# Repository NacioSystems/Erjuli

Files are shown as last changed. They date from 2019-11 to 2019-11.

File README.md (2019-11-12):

# Erjuli

## de NacioSystems:

Versión 3.0
Fecha: 5/11/2019

Este proyecto es robot de minisumo llamado **Erjuli**, pensado para las competiciones de un máximo de 500gr y dimensiones de 10x10cm2. Realizado por NacioSystems (O Milladoiro):

Es la tercera versión de este robot, la primera participó en la Oshwdem 2016, tenía una caja de madera y una balda desplegable, En la segunda versión se cambió la caja de madera por una impresa en 3D con PLA y se le añadió un micorservo en la parte trasera, para activar un brazo que bajaba la muleta que intentaba torear a los otros robots competidores. En esta tercera versión se eliminó la balda desplegable, por otra fija de material flexible pensada para el mismo efecto y se retocó el software para adaptarlo a las tres fases de la competición

- - -

### Introducción:

El chasis del vehículo está construido sobre la plataforma **Pololu Zumo Arduino**, sobre el que se instalaron sensores de distancia a través de ultrasonidos **HC-SR04**, uno en la dirección frontal y otro a cada lado del bastidor. Se complementa con el sensor **QTR** frontal de Pololu Zumo, que tendrá la función de detectar la línea del borde de la pista, con el objeto de no salirse.

El vehículo se enciende con el interruptor de la _shield_ de _Pololu_ y queda parado a la espera de que se pulse el botón incorporado en el chasis, para iniciar el combate. Una vez pulsado el botón **Erjuli** cuenta los 5 segundos de rigor que marcan las reglas. Una vez en marcha lee a través de los sensores en que situación está el contrincante, delante, a la derecha o a la izquierda. Lógicamente si no está en ninguna de esas posiciones es que estará detrás. **Erjuli** girará en la dirección en la que encuentre al contrincante y acelerará para embestirlo con sus 500gr de peso. Si en el movimiento detecta que pisa el borde de la pista, con los sensores delanteros QTR, retrocederá para salir de la zona  de peligro.

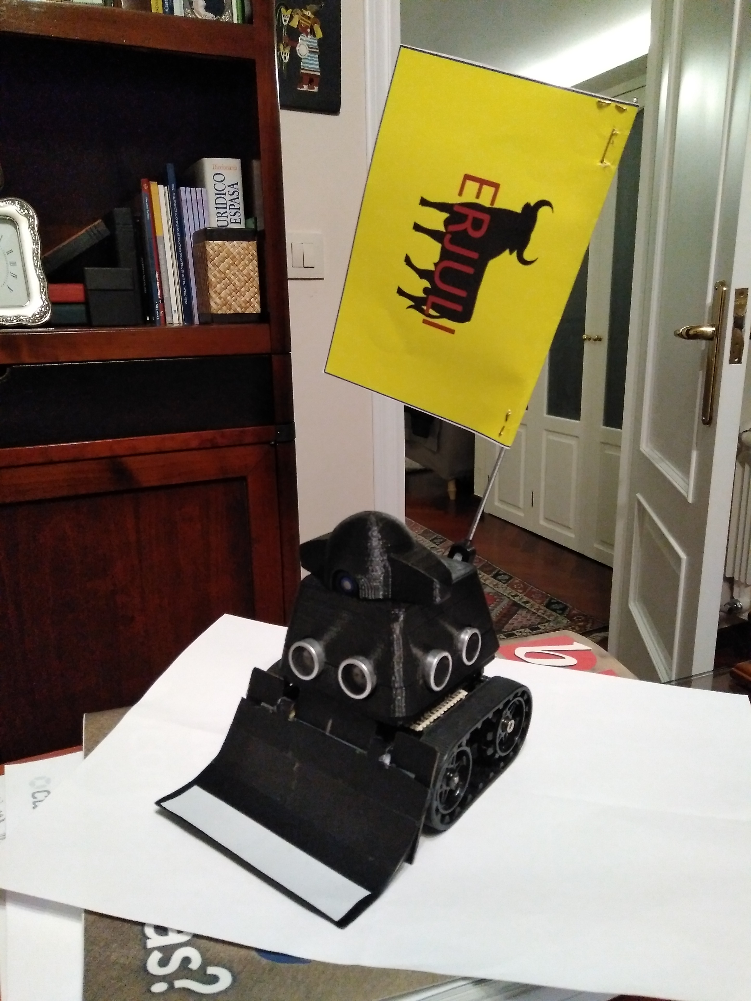
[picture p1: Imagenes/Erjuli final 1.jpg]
Erjuli Erjuli listo


Los sensores **HC-SR04** se activan simultáneamente a la vez, leyendo cada uno de ellos su propia señal y la de los otros sensores de modo sincronizado, hasta un rango de 50cm. Si detecta un objeto o contrincante en alguno de los lados, girará hasta detectarlo con el sensor frontal, pero este giro será por un tiempo limitado,para evitar quedarse en la misma posición expuesto al ataque del adversario.

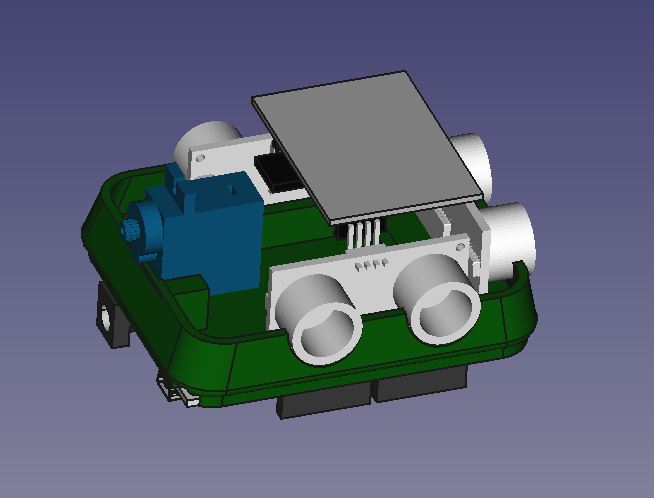
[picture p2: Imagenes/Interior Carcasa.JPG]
Sensores 3D Situación sensores


Al mismo tiempo **Erjuli** moverá su servomotor trasero, para poner la muleta del lado en que encuentra el adversario, para que este se confunda con el señuelo

### Materiales:

El vehículo utiliza los siguientes materiales:
* Pololu Zumo for Arduino con balda
* Arduino UNO R3
* 3 x HC-SR04
* Zumo Reflectante Sensor Array
* Microsergo SG90
* Piezas impresas en 3D PLA
* CI perforado universal para la conexión de los sensores de ultrasonidos
* Tiras de pines hembra y cableado para la conexión de todos los sistemas a la _shield_

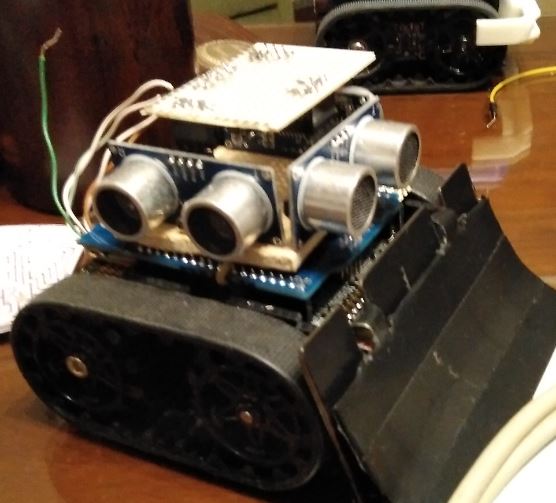
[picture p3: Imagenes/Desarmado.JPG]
Foto Erjuli desarmado Erjuli desarmado


Otros materiales:

Para ocultar toda la electrónica y cableado, así como para darle una mayor rigidez al conjunto, incluyendo la fijación del micorservo y su brazo para la muleta, se ha creado una caja impresa en 3D, que incluye los orificios para los sensores de ultrasonidos y el microservo SG90.

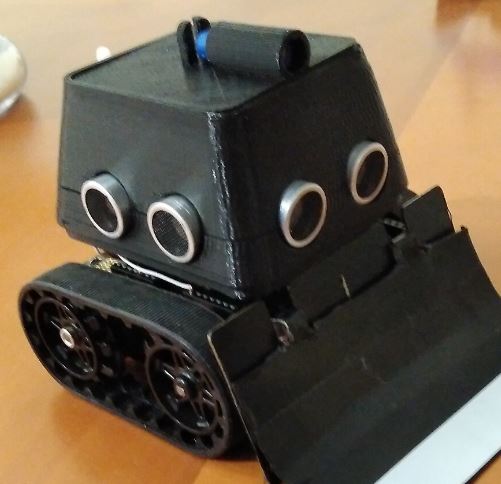
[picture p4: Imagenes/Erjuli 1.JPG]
Foto Erjuli 3D Erjuli 3D


### Dohyo:

El **_Dohyo_** es la pista donde se desenvuelve el combate de minisumo. Es una circunferencia de 77cm de diámetro de color negro. El borde exterior del _Dohyo_ es una línea blanca de 2,5cm de ancho y que sirve para indicarles a los robóts los límites que no se deben traspasar.

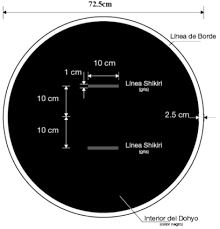
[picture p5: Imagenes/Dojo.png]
Foto Dohyo Medidas Dohyo


Durante cada combate cada robot intentará expulsar al otro del Dohyo, ganando el que quede dentro o salga en último lugar.

### Condiciones iniciales:

La competición se desenvuelve en hasta tres asaltos. En el primer asalto, los robots estarán enfrentados sobre unas marcas equiespaciadas del centro del _Dohyo_. En el segundo asalto los contrincantes estarán en la misma posición de inicio pero de tal manera que el lado derecho de uno será paralelo al lado izquierdo del otro, mirando en direcciones opuestas. En el tercer asalto, si no quedó claro cual es el vencedor en los dos primeros asaltos, los robots se pondrán de espaldas, mirando hacia el exterior del _Dohyo_.

Cada asalto comienza cuando lo indica el árbitro, dejando un espacio temporal de 5 segundos antes de empezar a moverse.

### Detección del contrincante y estrategia:
Erjuli, que torea por chicuelinas, localiza la posición del contrincante leyendo los sensores, de tal manera que si está enfrente acelerá para embestirlo, mientras le pasa unos muletazos a la embestida del rival. En el caso de que detecte al contrincante por uno de los flancos, moverá la muleta hacie ese flanco y girará al mismo tiempo dando un gran pase al rival y embistiendo una vez que lo tiene de frente. En caso de detectar el borde retrocederá y girará para mantenerse en el Dohyo.

En función del asalto, Erjuli empezará primero embistiendo de frente, para intentar obtener la mayor inercia posible en el choque inicial. En el segundo y tercer asalto, Erjuli girará para volver a embestir al contrincante una vez que lo encuentra de frente.

Erjuli utilizará su balda para levantar al otro contrincante y hacerle perder adherencia, para tener una posición dominante con su peso aumentado por el peso del otro robot levantado.

### Programa:

El programa está realizado con el IDE Arduino, para su programación directa a través de cable USB. En la carpeta software se puede ver el programa comentado. El programa cuenta con una pestaña de "configuración.h", para ajustar los valores por defecto, que dependerán de los motores y sensores utilizados en cada caso, si son diferentes a los de esta construcción.

Una vez encendido el robot configura los sensores, y dependiendo de las pulsaciones del botón de inicio sabrá en que estado estará, asalto primero, segundo o tercero. De esa manera puede empezar a moverse de diferente manera, es decir, en el primer asalto tendrá que avanzar para alcanzar la máxima velocidad lo antes posible para la colisión frontal con el adversario. Lógicamente ganará el que tenga mayor inercia (masa x velocidad) o el que consiga levantar al contrincante. Si lo levanta aumentará su peso y reducirá la adherencia del contrario.

La muleta del _Erjuli_ servirá para despistar al contrincante.

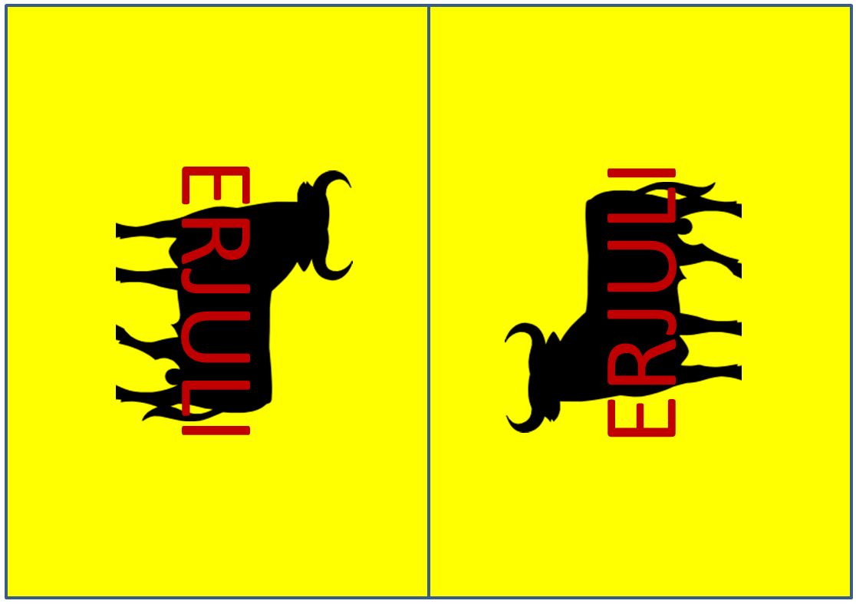
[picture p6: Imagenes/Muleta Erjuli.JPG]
Muleta Erjuli Diseño muleta Erjuli


### Construcción:
La construcción es sencilla, teniendo en cuenta el conexinado con la _shield Zumo_ y las piezas impresas en 3D. En el programa está la relación de conexión de los pines, que se refleja en el siguiente esquema:

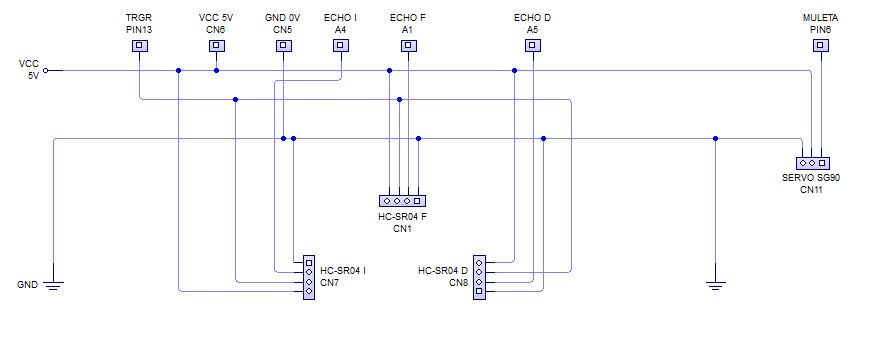
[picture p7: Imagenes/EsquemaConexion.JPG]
Esquema conexión Erjuli Esquema conexionado Erjuli


Es necesario desconectar el _jumper_ de medición de baterías de la _shield_, para utilizar el pin A1 para el _echo_ de uno de los sensores. Lo mismo con los puentes de **I2C** para gestión del giróscopo, acelerómetro y brújula, que dejan libres A4 y A5 para el mismo menester.

En la páctica compensa utilizar un protoboard tipo para instalar los sensores **HC-SR04** y el conector del microservo **SG90**, esto dará mayor fiabilidad a las conexiones y la fijación de los elementos físicos, que sufirán mucho en el combate

Esquema Zumo Shield Esquema de la Zumo Shield

La montera es opcional, se puede utilizar para el paseillo inicial, y dejarla fuera del _Dohyo_ durante el combate. Hay que tener en cuenta que la pérdida de una pieza de más de 5gr te puede dejar eliminado. Otra opción es pegar la montera a la cubierta de la carcasa con pegamento Imedio o similar, asegurando que no se perderán piezas durante la partida.

### Piezas impresas:

En la carpeta de piezas impresas están los modelos STL de la carcasa de _Erjuli_ donde se albergarán los senores **HC-SR04**, y el microservo. También están la montera, opcional, se puede llevar sólo para el paseíllo inicial, y el soporte que acopla el microservo al mástil de la muleta. 

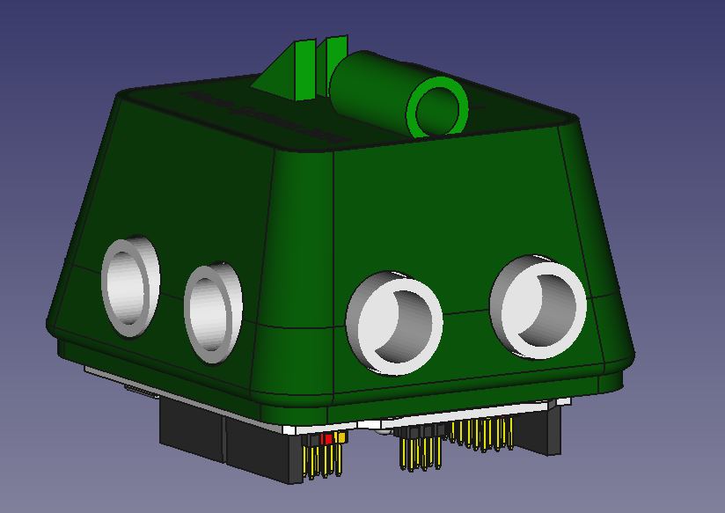
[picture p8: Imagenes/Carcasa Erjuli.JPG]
Carcasa Tseo


También se incluyen los ficheros FreeCad donde está el diseño de estas piezas.

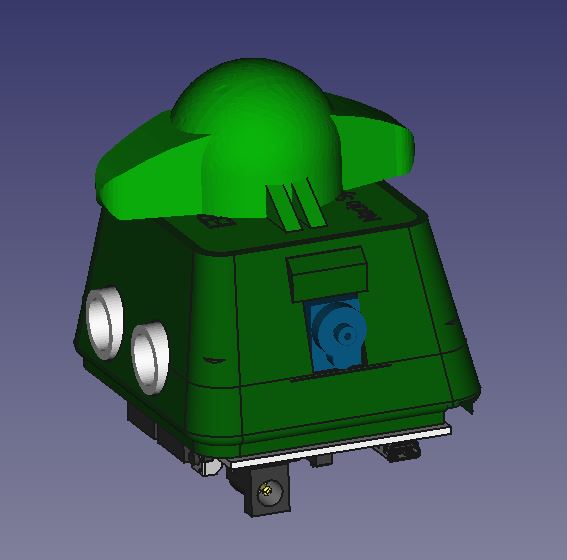
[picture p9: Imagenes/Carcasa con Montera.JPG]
Erjuli con montera


### Referencias:

* *[Página web OSHWDEM**][7]*
* *[Página Web reglamento Minisumo **OSHWDEM**][1]*
* *[Pololu Zumo for Arduino][2]*
* *[Arduino UNO R3][3]* 
* *[Pololu Zumo Reflectance Sensor Array][4]*
* *[Sensor de distancia HC-SR04 en BricoGeek][5]*
* *[Microservo SG90 en BricoGeek][6]*

### Autor:

**Ignacio Otero**

### Agradecimientos:

Muchas gracias **Bea** por tu colaboración en la revisión y corrección de esta página.

### Licencia:

Todos estos productos están liberados mediante Creative Commons Attribution-ShareAlike 4.0 International License.

[1]:http://rules.oshwdem.org/loita_sumo_es

[2]:https://www.pololu.com/product/2506
   
[3]:https://store.arduino.cc/arduino-uno-rev3

[4]:https://www.pololu.com/product/1419

[5]:https://tienda.bricogeek.com/sensores-distancia/741-sensor-de-distancia-por-ultrasonidos-hc-sr04.html

[6]:https://tienda.bricogeek.com/servomotores/968-micro-servo-miniatura-sg90.html

[7]:http://rules.oshwdem.org

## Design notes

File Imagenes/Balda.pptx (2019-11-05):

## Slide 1

ERJULI

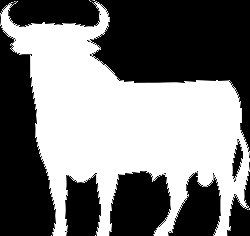
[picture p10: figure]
Toro blanco.svg

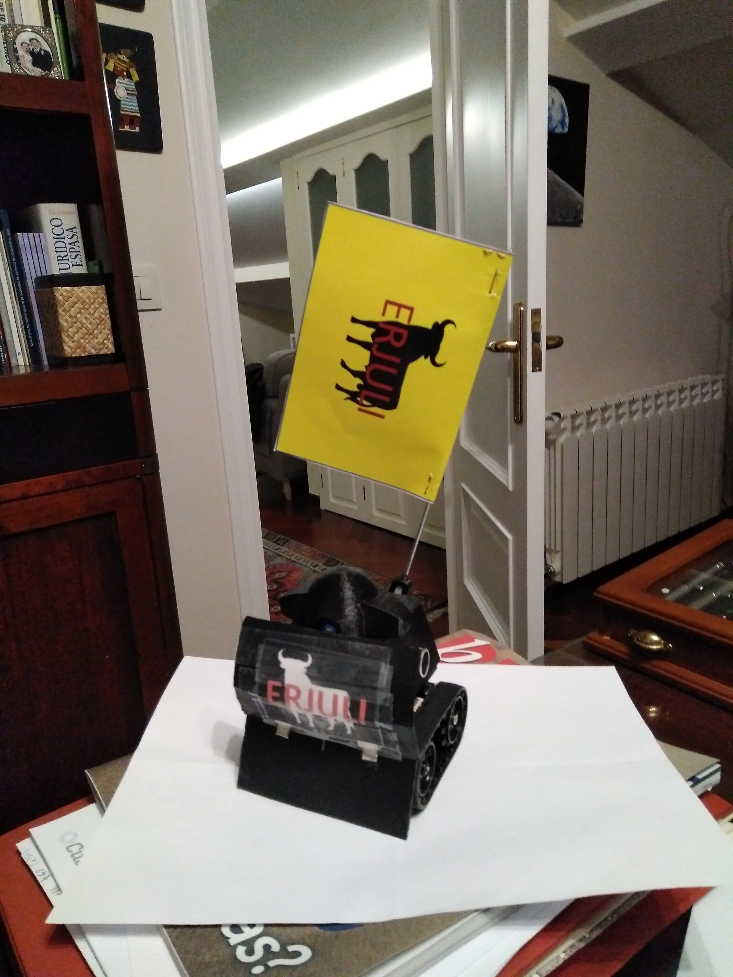
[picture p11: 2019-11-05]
Imagenes/Erjuli final 2.jpg

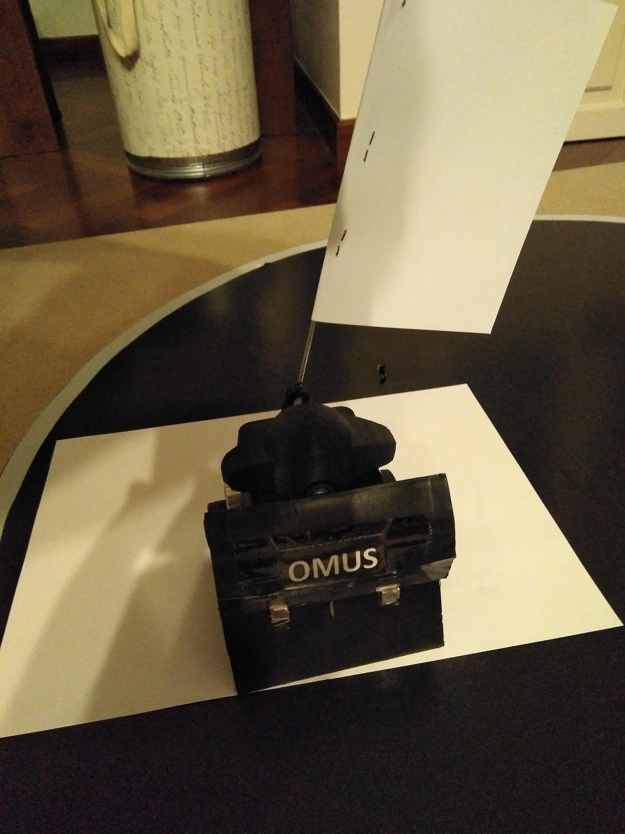
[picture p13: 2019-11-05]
Imagenes/Erjuli capote.jpg

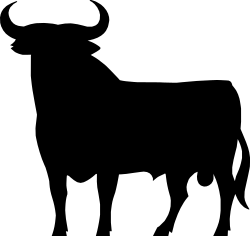
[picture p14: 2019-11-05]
Imagenes/250px-Toro_de_Osborne.svg.png

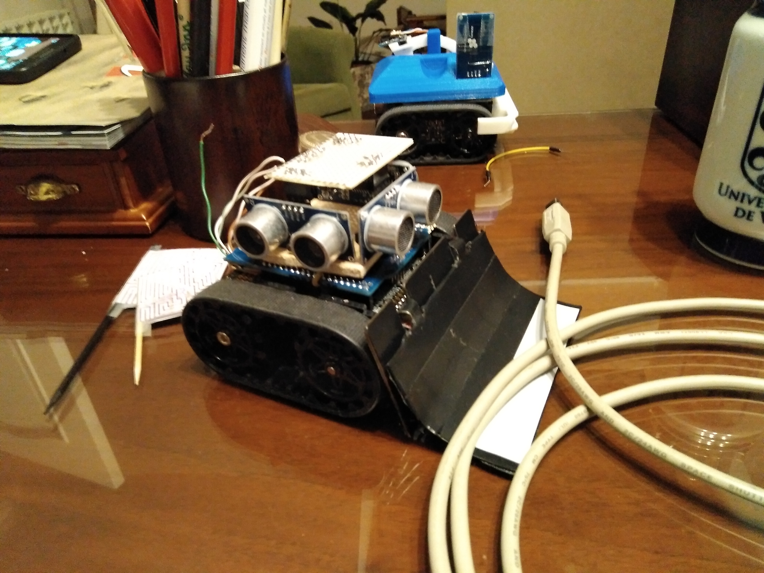
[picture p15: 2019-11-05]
Imagenes/Erjuli prototipo.jpg

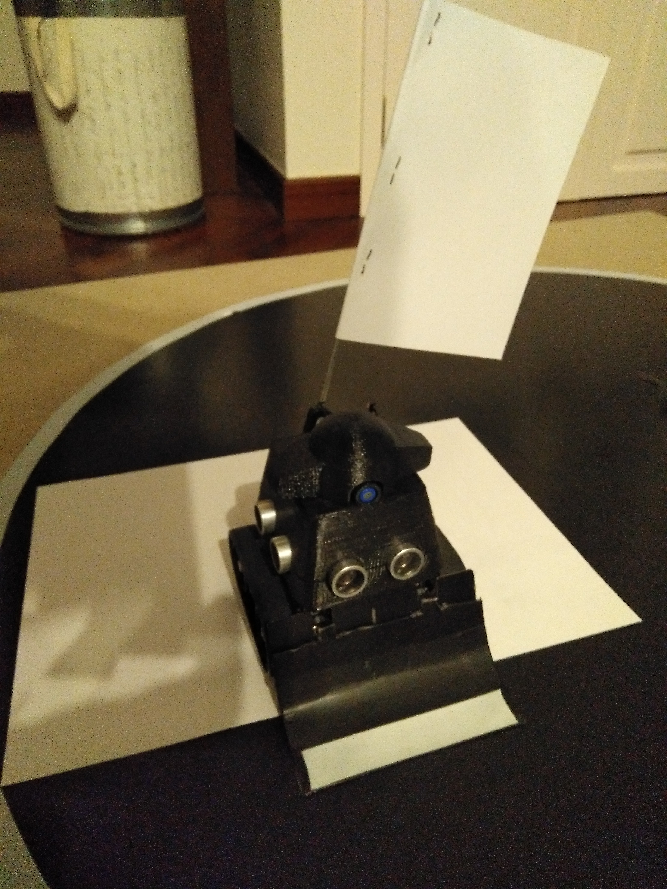
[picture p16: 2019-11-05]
Imagenes/Erjuli Capote 2.jpg

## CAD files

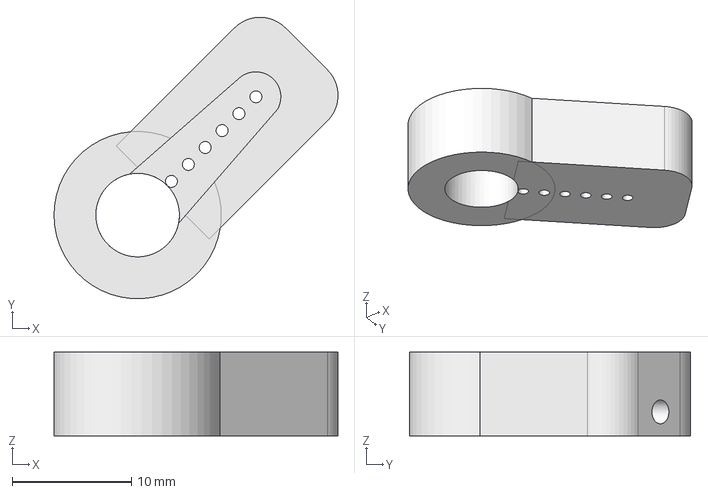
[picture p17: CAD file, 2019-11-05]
FreeCad/Soporte Muleta.FCStd
23.8 x 23.5 x 7.00 mm

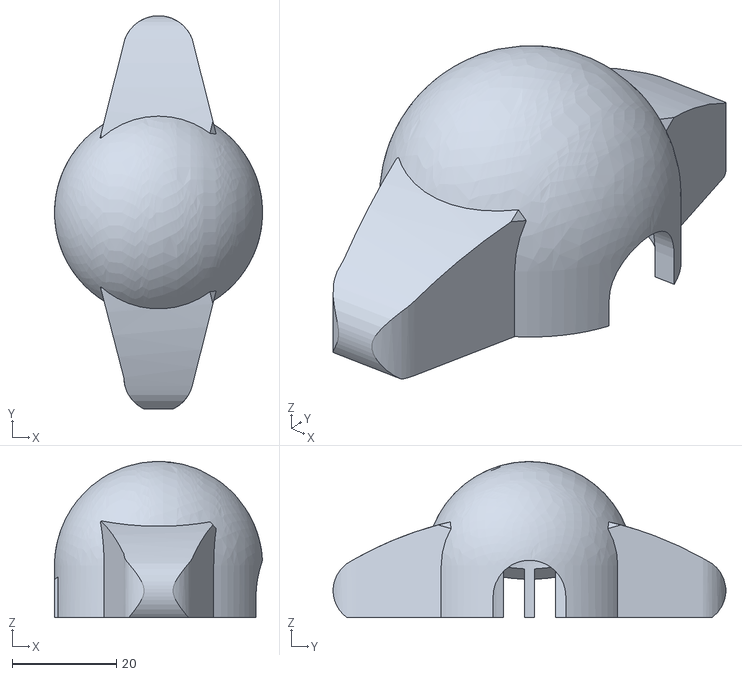
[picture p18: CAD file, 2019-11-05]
Partes impresas/Montera.stl
40.0 x 75.5 x 30.0

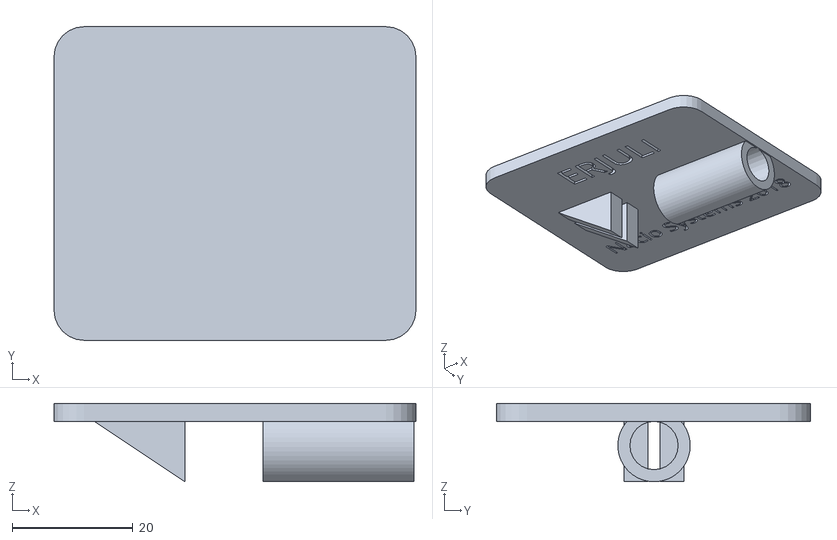
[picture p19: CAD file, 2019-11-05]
Partes impresas/Nueva tapa.stl
60.0 x 52.0 x 13.0

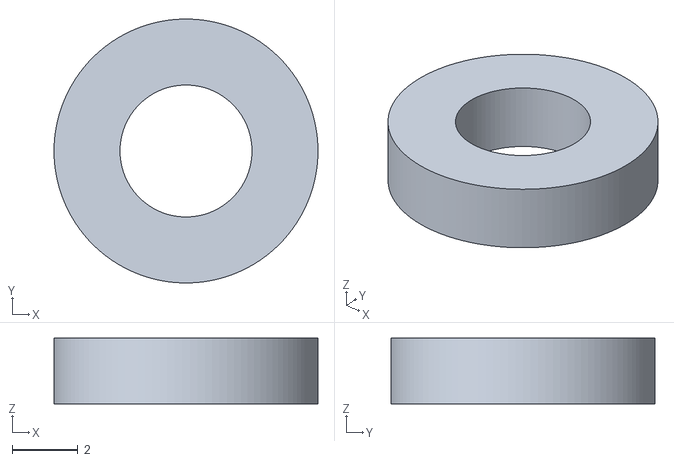
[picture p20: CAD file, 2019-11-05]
Partes impresas/Separadores tornillos.stl
8.00 x 8.00 x 2.00

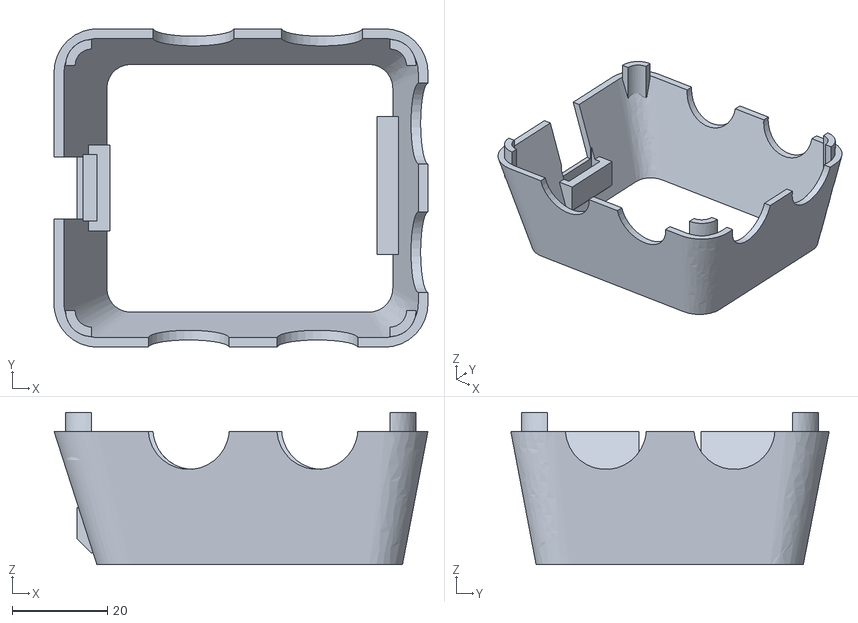
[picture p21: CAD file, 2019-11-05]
Partes impresas/Nueva parte superior.stl
78.5 x 66.8 x 32.0

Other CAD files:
Partes impresas/Soporte Muleta.stl

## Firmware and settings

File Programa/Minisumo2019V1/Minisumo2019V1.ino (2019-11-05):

// *******************************************************************************************************
// *******************************************************************************************************
// ************  PROGRAMA LUCHA SUMO DE IGNACIO OTERO CONCURSO OSHWDEM 2019 CORUÑA           *************
// *******************************************************************************************************
// *******************************************************************************************************
// ************       NOMBRE PROPUESTO DEL BICHO OMUS               modificaciones 2018      *************
// *******************************************************************************************************
// *******************************************************************************************************

// Idea original de Pololu, adaptado por Ignacio Otero
// Versión del 2 de noviembre, doble pitido al encender y escaneo US tres veces por segundo
// Partimos de la version del 17/2/2016 que funcionaba bien.
// Velocidad, siempre a la máxima
// con excepción de la marcha atrás.
// Version 15/10/2018, cambiamos placa US y pasamos el disparo a A1
// Cambio motores por otros más rápidos de José Miguel
// 2/11/2018 incorporo microservo para manejar muleta,controlado por 6PWM
// 3/11/2018 Cambiar la alimentación del serrvo a Vin, se cuelga con 5vcc
// 9/11/2018 Elimino el movimiento de muleta en la detección y le meto 64gr de plomo
// y amplio el tiempo de giro a 700ms

// Comentario del día siguiente: 11/11/2018
// Se me olvidó el sensor de líneas en el coche!
// No me di cuenta hasta el segundo combate
// En cualquier caso funionó bien sin cosas raras, salvo que se salía por la borda
// Hubiese quedado en un honrroso 3er puesto de tener sensor.
// Hubiese quedado cuarto de no arrancar el el último combate de espaldas.
// Propongo volver con el armazón más sujeto, cambiar el detector de ultirasonidos por Pololu U32A

// IMPORTANTE DESCONECTAR PUENTES EN PLACA ZUMO PARA SENSORES PROXIMIDAD
// Liberamos lector de batería, A1
// Desconexión giroscopo y acelerometro, liberamos pines A4 y A5, los usamos para ultrasonidos
// Esta es la version ultrasonidos 13 y A1, los usamos para ultrasonidos
// Es necesaria una versión distinta para detectores ópticos
// El 6 queda disponible PWM para servo

// PINES USADOS EN ESTA VERSIÓN (15)
// Motores Zumo (4) = 7, 8, 9, 10
// Sensor IR Zumo (7) = A0, A2, A3, 2, 4, 5, 11
// Buzzer Zumo (1) = 3
// Pulsador Pushbutton Zumo (1) = 12
// Ultrasonidos disparo (1) = 13 (led)
// Ultrasonidos Echo centro, izquirda y derecha (3) A1, A4, A5
// Servo a través de pin (1) = 6
// ***********************************************************************************

// CAMBIOS 2019
// Pegar carcasa superior
// Pasar todos los define a configuración
// Poner un estado de arrancada, de frente, de lado y hacia atrás
// Desconectar sensores IR mientras se maneja el servo en la arrancada
// Durante un periodo de tiempo, lo que tarda en bajar el servo:
//       - Posición de frente. Arrancar a máxima velocidad y bajar el servo
//       - Posición de lado. Girar un tiempo, bajar el servo y adelante a máxima
//       - Posición hacia atrás. Girar más tiempo, bajar el servo y a máxima
// A partir de aqui el servo no se toca y se maneja la librería IR ZumoReflectanceSensorArray

/* Este ejemplo utiliza el sensor de bordes del Zumo y su librería para evitar salir del área circular
 * del Dohyo. Además utiliza las librerías de ZumoMotors, PushButton, ZumoBuzzer y Ultrasonic
 *
 *
 * Este programa tiene las siguientes rutinas:
 *
 *  - utiliza el PushButton para comenzar la partida, cuenta atrás y detener el robor
 * 
 *  - utiliza el ZumoBuzzer para tocar efectos de sonido en la competición
 *  
 *  - utiliza QTRSensors y ZumoReflectanceSensorArray para leer los IR de línea
 *  
 *  - utiliza Ultrasonic para leer los sensores de ultrasonidos
 *
 *  - tiene un aleatorizador de tiempo para los giros, evitando seguir un patrón
 *
 */



// LIBRERÍAS
#include "Configuracion.h" // En esta pestaña están los parámetros configurables
#include <ZumoBuzzer.h> // Para las melodías y pitidos
#include <ZumoMotors.h> // Controla los motores
#include <Pushbutton.h> // Pulsador de inicio y parada
#include <QTRSensors.h> // Necesita esta librería para la libreria del sensor de reflectancia
#include <ZumoReflectanceSensorArray.h> // Sensores delanteros de línea
#include <Ultrasonic.h> // Para la versión del detector US
#include <Servo.h>      // Para manejar la "muleta" de engaño y bajar la balda

 
// Definimos una clase de ultrasonidos derecha(Trig Pin, Echo Pin)
Ultrasonic detectorUS(GATILLO, sensor_US_centro); 
Ultrasonic detectorIZ(GATILLO, sensor_US_izquierda); 
Ultrasonic detectorDR(GATILLO, sensor_US_derecha); 

// Definimos una clase de boton del Zumo
Pushbutton pulsador(ZUMO_BUTTON); // En la librería Pushbutton ya se define el pin ZUMO_BUTTON 

// Definimos una clase de sernsor reflectante frontal, sin pin de emisión, no apaga los IR Leds
ZumoReflectanceSensorArray sensorIR(QTR_NO_EMITTER_PIN); 

// Definimos una clase de Zumo Motors 
ZumoMotors motores;

// Definimos una clase de Zumo Buzzer para el sonido
ZumoBuzzer zumbador;

// Definimos una clase de servo para la muleta
Servo muleta; 

// Variables generales
unsigned int valores_sensor[NUM_SENSORES]; // Un array de 6 valores enteros sin signo

int Pos_Capote=Capote_AR; //Es la posición del Capote, inicialmente a 90

// EFECTOS DE SONIDO
const char efecto_sonido[] PROGMEM = "O4 T100 V12 L4 MS g12>c12>e12>G6>E12 ML>G2"; // Melodía de "A la carga..."
 // El sonido se desactiva con V0, para suprimirlo y V15 para el máximo volumen
 
// Esta variable la utilizamos en el loop principal y varias funciones
int direccion = RECTO;
boolean detectado =false;
int distancia=80;
int distancia_IZ=0;
int distancia_DR=0;
unsigned long TiempoGiro=0;
unsigned long PeriodoServo=0; // Intervalo de tiempo para controlar los 20ms del periodo del servo



// CONFIGURACION INICIAL
void setup()
   {  
  
       Serial.begin(57600); // Iniciamos puerto serie pero no se utiliza
       Serial.println("Inicializando.....");
       Serial.println("Pulsa el boton de inicio:?");
       zumbador.playNote(NOTE_G(3), 50, 12); // Toca nota
       delay(250);
       zumbador.playNote(NOTE_G(3), 50, 12); // Toca nota

       // Crea una semilla para hacer el aleatorizador
       randomSeed((unsigned int) millis());
  
       // Comentar las siguiente líneas si es necesario cambiar el sentido de giro de los motores
       //motores.flipLeftMotor(true);
       //motores.flipRightMotor(true);

       // Colocamos la muleta en el pin 6 PWM
       muleta.attach(PinMuleta);

       // La muleta debe estar hacia arriba al empezar
       muleta.write(Capote_AR);
    

       pinMode(LED, OUTPUT); // Ponemos el pin 13 del LED y del gatillo como salida
       
       zumbador.playMode(PLAY_AUTOMATIC); // El sonido está en modo automático
       
       // Espera inicialmente a que se pulse el botón
       PulsarCuentaAtras(false); // Y esperamos a que se toque el botón
   }



// BUCLE PRINCIPAL
void loop()
{

  // Cuando se pulsa por segunda vez en competición, para el robot para reiniciar
  if (pulsador.isPressed()) 
     {
        motores.setSpeeds(0, 0); // Paramos motor
        pulsador.waitForRelease(); // Espera a que se suelte el botón
        // Espera de nuevo a que se pulse el botón para iniciar otra ronda
        PulsarCuentaAtras(true); // Hace la cuenta atrás inicial
     }
  
   sensorIR.read(valores_sensor); // Leemos el array de sensores
   //direccion=RECTO;     // Por defecto en cada bucle la direccion es RECTO
  
  // COMPRUEBA QUE TOCAMOS EL BORDE PARA CAMBIAR DE SENTIDO, CON FONDO NEGRO Y LINEAS BLANCAS
  if (valores_sensor[0] < NIVEL_DISPARO_QTR) // Comprobamos que el sensor de izquierda está en la línea blanca
     { // Si el sensor de la izquierda detecta la línea blanca, entonces retrocede un poco y gira a la derecha
        direccion=DERECHA;
        giro(direccion, true); // La función giro incluye la marcha atrás y despues giro
        busca(direccion);
     }
     
  else if (valores_sensor[5] < NIVEL_DISPARO_QTR) // Ahora comprobamos el de la derecha, que no esté en la línea
     {      // Si el sensor de la derecha detecta la línea blanca, entonces retrocede un poco y gira a la izquierda
       direccion=IZQUIERDA;
       giro(direccion, true); // Giro izquieda, antes un poco atrás
       busca(direccion);
     }

  // Cuatro veces por segundo leemos sensores US y tomamos decisión
  if(millis()-TiempoGiro>330)
    {
        //direccion=RECTO; // Por defecto Recto
        direccion=DimeDireccion(); // La función mira a través de ultrasonidos y devuelve la dirección del objeto
        TiempoGiro=millis();
    }
  
  // LLamamos a ls funcion de busqueda por US, en funcion de la dirección
  // Se encarga de mover los motores en esa direccion
  busca(direccion); // Y si detecta algo de frente empuja recto siempre
        
  } // Fin del bucle principal




// FUNCIÓN PULSAR Y CUETA ATRÁS
// Esta función cuenta hasta 5 segundos, despues de pulsar el boton
void PulsarCuentaAtras(bool restarting)
   { 

     digitalWrite(LED, HIGH); // Activa el LED para avisar que está esperando
     pulsador.waitForButton();  // a que se pulse el boton
     digitalWrite(LED, LOW);  // Una vez pulsado apaga el LED
   
     // Cuenta hasta 3, 3 segundos
     for (int i = 0; i < 3; i++)
      {
        delay(1000); // Un segundo
        zumbador.playNote(NOTE_G(3), 50, 12); // Toca nota
        Serial.println(5-i);
      }

    delay(1000); // Otro segundo
    Serial.println("2   Preparados----!");
    zumbador.playFromProgramSpace(efecto_sonido); // Sonido de a la carga
    delay(1000); // Otro segundo, en total 5.
    Serial.print("1    ");
    Serial.println("A LA CARGA....!");
    
  }





// FUNCION GIRO, ESTA FUNCIÓN SE ACTIVA AL TOCAR LOS BORDES
// IDICAR LA DIRECCIÓN DERECHA O IZQUIERDA
// RAMDOMIZE es para mejorar la búsqueda con tiempo aleatorio.
void giro(int direction, bool semilla_ramdom)
   {
  
     static unsigned int incremento_tiempo = TIEMPO_GIRO / 4; // Unos 35ms

     motores.setSpeeds(-RETROCESO, -RETROCESO); // Marcha atrás
     delay(TIEMPO_RETROCESO);                   // Retrocede 200ms
  
     motores.setSpeeds(AVANCE * direction, -AVANCE * direction); // Gira derecha o irzquierda
     delay(semilla_ramdom ? TIEMPO_GIRO + (random(8) - 2) * incremento_tiempo : TIEMPO_GIRO); // El tiempo de giro es aleatorio
 
     motores.setSpeeds(AVANCE, AVANCE);

   }





// FUNCION BUSCA CON SENSOR ULTRASONIDOS
// Busca enemigo en un sentido derecha o izquierda
// Busca y Gira hasta que encuentra un objeto
// Se puede mejorar para que avance un poco y haga círculos
void busca(int direction)
  {
    // Avanzamos si es recto, en caso de izq o der, giramos hasta encontrar algo
    // Como mucho 600ms, despues salimos avanzando de nuevo
    unsigned long tiempo=0;
    tiempo=millis(); // Tomamos nota del tiempo para que no nos pasemos de 0,8 segundos
    int distancia=80;
   
    if(direction!=RECTO) // En caso de que NO busquemos hacia adelante
          { // Mientras la distancia es más de 50 y no superamos 1 segundo
            while((distancia=detectorUS.Ranging(CM)>ALCANCE)&&(millis()-tiempo<TIEMPO_BUSCA)) // Antes giraba hasta 1200
               { // GIRAMOS HASTA ENCONTRAR ALGO O COMO MÁXIMO 1,0 SEGUNDOS
                 motores.setSpeeds(AVANCE * direction, -AVANCE * direction);
               }
           }
     motores.setSpeeds(AVANCE, AVANCE); // Salimos avanzando de la busqueda

  }// Fin de la funcion


// FUNCION DIME DIRECCION
// DEVUELVE LA DIRECCION EN FUNCION DE LA LECTURA DE LOS SENSORES US
int DimeDireccion()
{
     // Leemos los tres sensores para ver si detecta algo
     distancia=detectorUS.Ranging(CM);
     delay(10); // Esperamos 10 ms para evitar ecos
     distancia_IZ=detectorIZ.Ranging(CM);
     delay(10); // Esperamos 10 ms para evitar ecos
     distancia_DR=detectorDR.Ranging(CM);
     delay(10); // Esperamos 10 ms para evitar ecos

     if (distancia<=ALCANCE) 
        {
          Serial.print("Objetivo RECTO cm ");
          Serial.println(distancia);
          return RECTO; // Si está defrente devuelve Recto
        }        
     if (distancia_IZ<=ALCANCE) 
        { 
          Serial.print("Objetivo IZQUIERDA cm ");
          Serial.println(distancia_IZ);
          return IZQUIERDA; // Si está a la izquierda devuelve Izquierda
        }
     if (distancia_DR<=ALCANCE) 
        {
          Serial.print("Objetivo DERECHA cm ");
          Serial.println(distancia_DR);
          return DERECHA; // Si está a la derecha devuelve Derecha
        }
     if ((distancia>ALCANCE)&&(distancia_IZ>ALCANCE)&&(distancia_DR>ALCANCE)) 
        { 
          Serial.println("Sin Objetivo"); // Puede estar detrás
          return RECTO; // cambiar por un giro
        }
        
  }
    

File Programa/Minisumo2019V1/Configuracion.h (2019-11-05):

// PINES FIJOS QUE NO ESTÁN EN LIBRERÍAS
#define LED 13     // Lo usamos para led
#define GATILLO 13 // Es el mismo que el led y los usamos para el disparo de US

#define sensor_US_izquierda A4 // Sensor de ultrasonidos de la izquierda
#define sensor_US_derecha   A5 // Sensor de ultrasonidos de la derecha
#define sensor_US_centro    A1 // Sensor de ultrasonidos central

// PARÁMETROS DEL SENSOR REFLECTANTE IR FRONTAL
#define NUM_SENSORES 6 // Es el número de sensores a utilizar en el sensor IR, todos
#define NIVEL_DISPARO_QTR  300 // Es el valor de decisión, en microsegundos, tenía anteriormente 300 para borde blanco, 900 cartón marrón borde negro
                               // Hay que pensar que el Dohyo es negro y la línea blanca


// PARÁMETROS DEL MOTOR, DEBEN AJUSTARSE EN FUNCIÓN DEL MOTOR
// Velocidades
#define RETROCESO         200 // 0 parado, 400 máxima velocidad
#define AVANCE            400
#define TIEMPO_RETROCESO  400 // Con el anterior motor estaba a 200 ms
#define TIEMPO_GIRO       150 // Con el anterior motor estaba a 150 ms (600)
#define TIEMPO_BUSCA     1000 // Tenía 700

// Giros
#define DERECHA 1        // Multiplica por la velocidad por eso cambia de signo
#define IZQUIERDA -1
#define RECTO 0
#define CURVA 2          // No se utiliza

// Distancia de alcance en cm
#define ALCANCE 49

// Muleta
#define PinMuleta 6
#define Capote_DR 50
#define Capote_IZ 140
#define Capote_AR 90
